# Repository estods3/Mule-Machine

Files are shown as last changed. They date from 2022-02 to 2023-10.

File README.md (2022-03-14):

# mule_machine
A drinkbot for making Moscow Mules

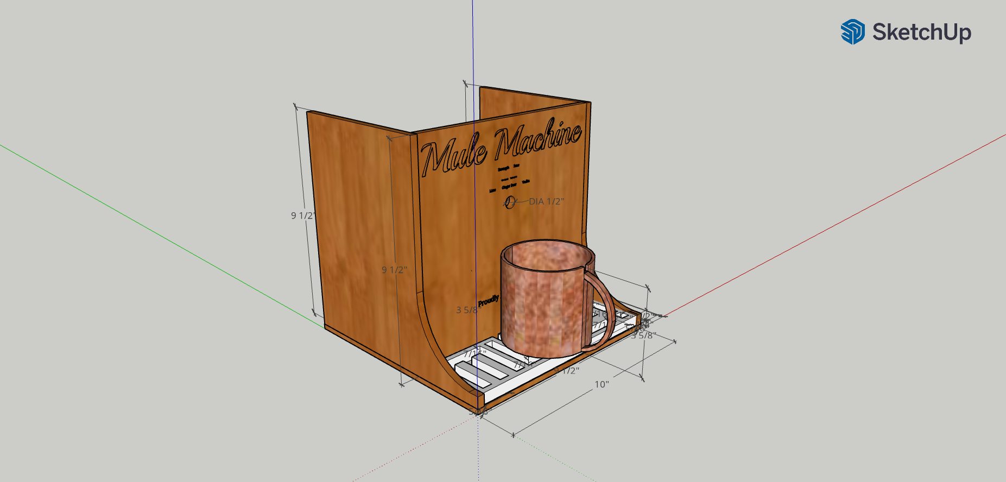
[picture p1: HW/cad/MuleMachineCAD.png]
CAD Assembly
[]()

## Design File Structure

### SW
ATmega328 microcontroller code.
  * Pin Assignments
  * Bootup Animation
  * Standby Animation
  * Potentiometer Calibration Controls
  * Cup-Sensor Detection
  * Pump Control and LED animation

### HW

#### cad

Sketchup File - 3D model

[CAD Assembly]()

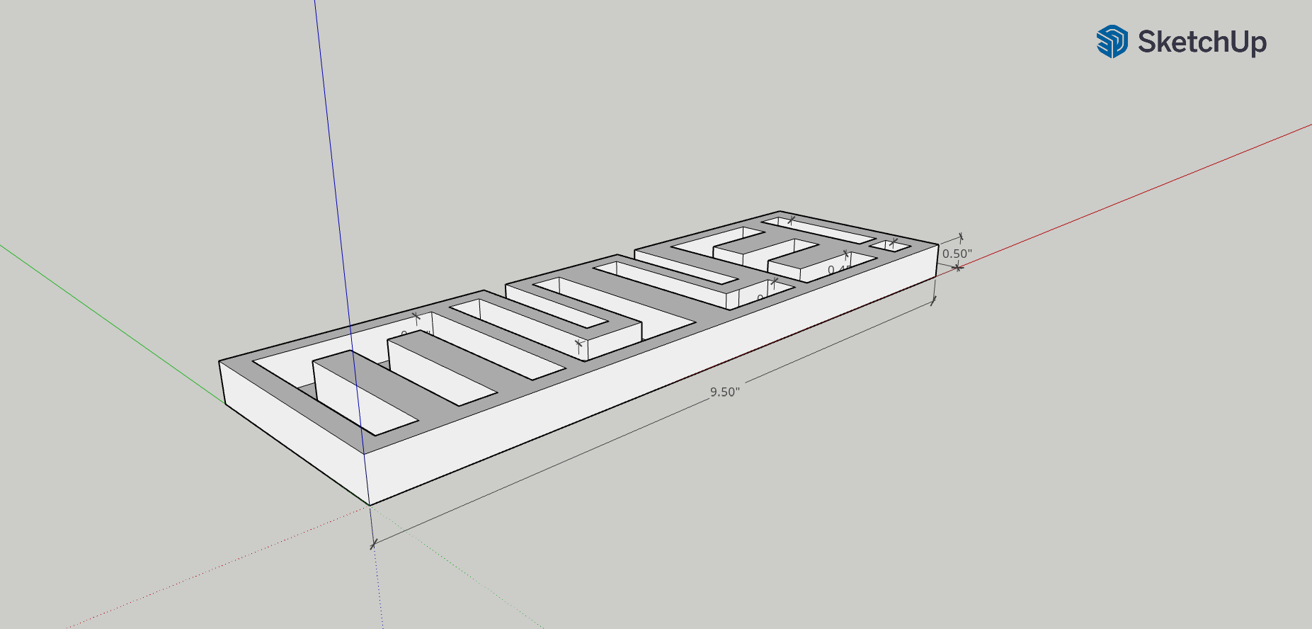
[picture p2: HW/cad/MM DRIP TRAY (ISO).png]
DRIP TRAY ISO
[]()
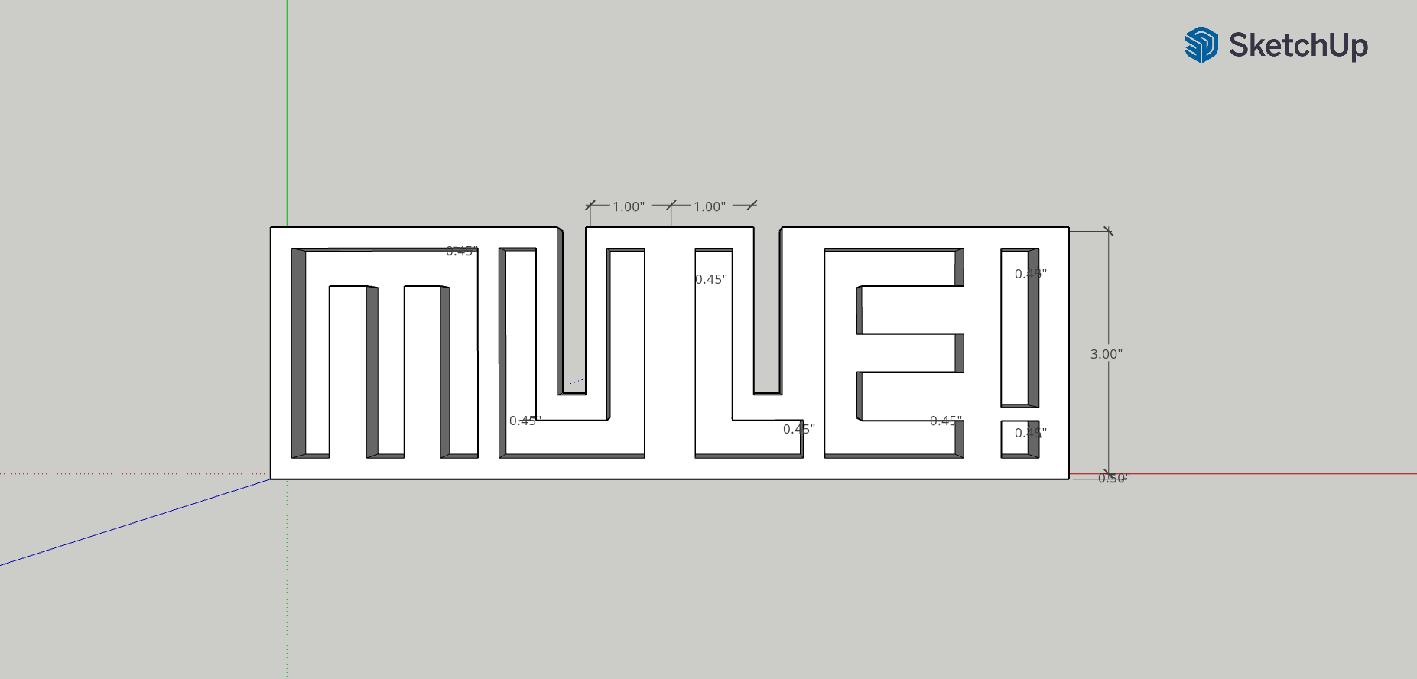
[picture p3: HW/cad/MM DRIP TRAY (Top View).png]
DRIP TRAY Top View
[]()

LightBurn laser engraved part files (Coming Soon)

3D printed part files
* MM DRIP TRAY.STL 

#### pcb

Eagle Schematic file

Eagle board layout file

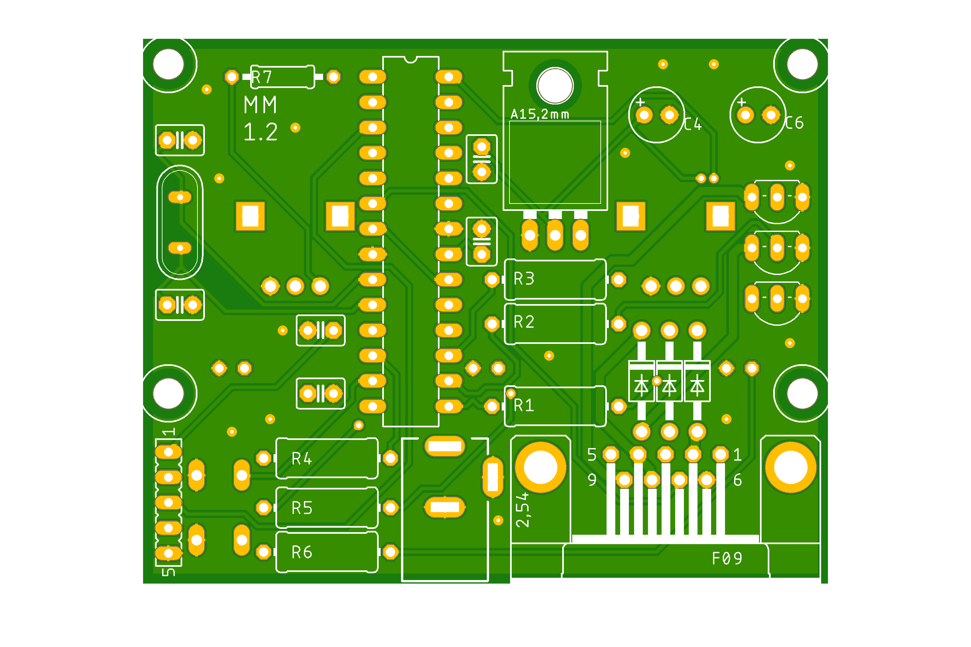
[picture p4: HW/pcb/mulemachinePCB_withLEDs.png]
PCB Top
[]()
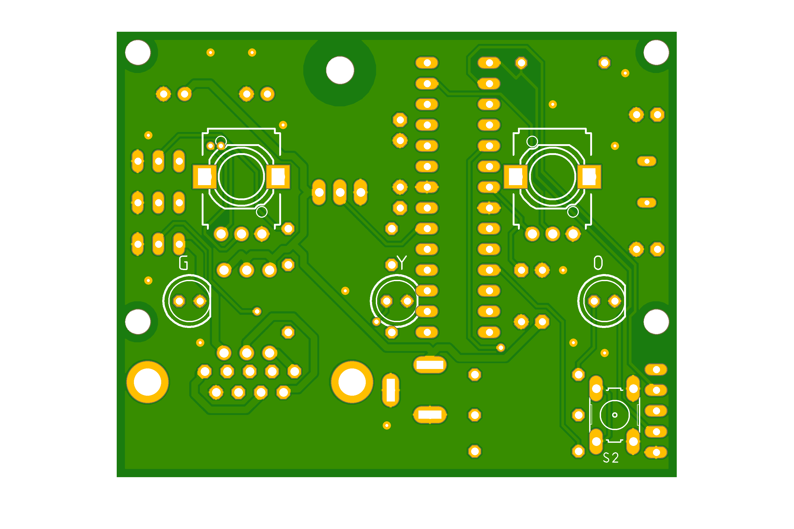
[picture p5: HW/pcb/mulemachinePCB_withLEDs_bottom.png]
PCB Bottom
[]()

associated gerber files (manufacturing)

parts list/BOM

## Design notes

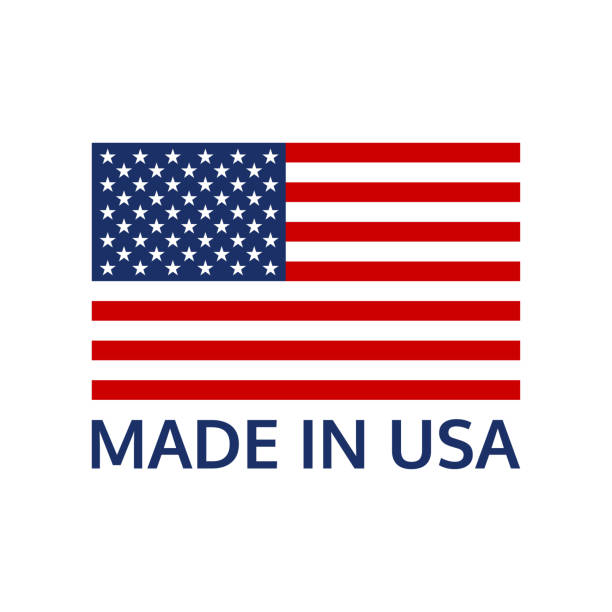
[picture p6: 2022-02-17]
HW/laser/american_flag.jpg

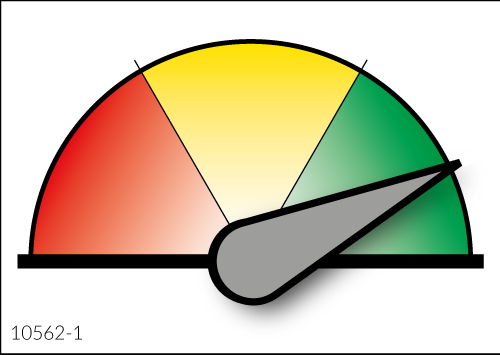
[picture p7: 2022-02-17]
HW/laser/gauge.png

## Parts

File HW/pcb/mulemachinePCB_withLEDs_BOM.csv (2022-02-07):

Part | Value | Device | Package | Description | MF | MPN | OC_FARNELL | OC_NEWARK | POPULARITY | SPICEPREFIX
C1 | 470uF | C2,5-3 | C2.5-3 | CAPACITOR |  |  |  |  | 38
C2 | 22pF | C2,5-3 | C2.5-3 | CAPACITOR |  |  |  |  | 38
C3 | 22pF | C2,5-3 | C2.5-3 | CAPACITOR |  |  |  |  | 38
D1 | 1N4004 | 1N4004 | DO41-10 | DIODE |  |  |  |  | 82
D2 | 1N4004 | 1N4004 | DO41-10 | DIODE |  |  |  |  | 82
D3 | 1N4004 | 1N4004 | DO41-10 | DIODE |  |  |  |  | 82
IC1 | LD117AV50 | LD117AV50 | TO220L1 | Low drop fixed and adjustable positive voltage regulators 1 A |  |  |  |  | 0
IC2 | MEGA8-P | MEGA8-P | DIL28-3 | MICROCONTROLLER |  |  | unknown | unknown | 17
J1 | DCJ0202 | DCJ0202 | DCJ0202 | DC POWER JACK |  |  | unknown | unknown | 17
LED1 |  | LED5MM | LED5MM | LED |  |  |  |  | 93
LED2 |  | LED5MM | LED5MM | LED |  |  |  |  | 93
LED3 |  | LED5MM | LED5MM | LED |  |  |  |  | 93
Q1 |  | XTAL/S | QS | CRYSTAL |  |  |  |  | 59
R1 | 150 | R-US_0204/7 | 0204/7 | RESISTOR, American symbol |  |  |  |  | 48 | R
R2 | 150 | R-US_0204/7 | 0204/7 | RESISTOR, American symbol |  |  |  |  | 48 | R
R3 | 150 | R-US_0204/7 | 0204/7 | RESISTOR, American symbol |  |  |  |  | 48 | R
R4 | 200 | R-US_0204/7 | 0204/7 | RESISTOR, American symbol |  |  |  |  | 48 | R
R5 | 200 | R-US_0204/7 | 0204/7 | RESISTOR, American symbol |  |  |  |  | 48 | R
R6 | 200 | R-US_0204/7 | 0204/7 | RESISTOR, American symbol |  |  |  |  | 48 | R
R7 | 200 | R-US_0204/7 | 0204/7 | RESISTOR, American symbol |  |  |  |  | 48 | R
S1 | RDT1034 | RDT1034 | RDT1034 | PUSH SWITCH |  |  |  |  | 4
SV1 |  | FE05-1 | FE05-1 | FEMALE HEADER |  |  | unknown | unknown | 7
T1 |  | MPS2222A-NPN-TO92-CBE | TO92-CBE | NPN Transistror |  |  |  |  | 0
T2 |  | MPS2222A-NPN-TO92-CBE | TO92-CBE | NPN Transistror |  |  |  |  | 0
T3 |  | MPS2222A-NPN-TO92-CBE | TO92-CBE | NPN Transistror |  |  |  |  | 0
X2 |  | F09HP | F09HP | SUB-D |  |  | unknown | unknown | 2

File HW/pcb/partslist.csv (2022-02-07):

Partlist
Exported from mulemachinePCB_withLEDs.sch at 2/1/22 5:24 PM
EAGLE Version 9.6.2 Copyright (c) 1988-2020 Autodesk, Inc.
Assembly variant:
Part     Value          Device                Package  Library        Sheet
C1       470uF          C2,5-3                C2.5-3   capacitor-wima 1
C2       22pF           C2,5-3                C2.5-3   capacitor-wima 1
C3       22pF           C2,5-3                C2.5-3   capacitor-wima 1
D1       1N4004         1N4004                DO41-10  diode          1
D2       1N4004         1N4004                DO41-10  diode          1
D3       1N4004         1N4004                DO41-10  diode          1
IC1      LD117AV50      LD117AV50             TO220L1  v-reg          1
IC2      MEGA8-P        MEGA8-P               DIL28-3  atmel          1
J1       DCJ0202        DCJ0202               DCJ0202  con-jack       1
LED1                    LED5MM                LED5MM   led            1
LED2                    LED5MM                LED5MM   led            1
LED3                    LED5MM                LED5MM   led            1
Q1       16Mhz          XTAL/S                QS       special        1
R1       150            R-US_0207/10          0207/10  rcl            1
R2       150            R-US_0207/10          0207/10  rcl            1
R3       150            R-US_0207/10          0207/10  rcl            1
R4       200            R-US_0207/10          0207/10  rcl            1
R5       200            R-US_0207/10          0207/10  rcl            1
R6       200            R-US_0207/10          0207/10  rcl            1
R7       200            R-US_0207/10          0207/10  rcl            1
R8       1k ohms        TRIM_EU-B25P          B25P     pot            1
R9       1k ohms        TRIM_EU-B25P          B25P     pot            1
S1       RDT1034        RDT1034               RDT1034  switch         1
SV1                     FE05-1                FE05-1   con-lsta       1
T1                      MPS2222A-NPN-TO92-CBE TO92-CBE transistor     1
T2                      MPS2222A-NPN-TO92-CBE TO92-CBE transistor     1
T3                      MPS2222A-NPN-TO92-CBE TO92-CBE transistor     1
X2                      F09HP                 F09HP    con-subd       1

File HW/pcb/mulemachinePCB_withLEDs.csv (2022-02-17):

Part | Value | Device | Package | Description | MF | MPN | OC_FARNELL | OC_NEWARK | POPULARITY | SPICEPREFIX
C1 | 0.1uF | C2,5-3 | C2.5-3 | CAPACITOR |  |  |  |  | 38
C2 | 22pF | C2,5-3 | C2.5-3 | CAPACITOR |  |  |  |  | 38
C3 | 22pF | C2,5-3 | C2.5-3 | CAPACITOR |  |  |  |  | 38
C5 | 470uF | CPOL-US153CLV-0605 | 153CLV-0605 | POLARIZED CAPACITOR, American symbol |  |  |  |  | 8 | C
D1 | 1N4004 | 1N4004 | DO41-10 | DIODE |  |  |  |  | 82
D2 | 1N4004 | 1N4004 | DO41-10 | DIODE |  |  |  |  | 82
D3 | 1N4004 | 1N4004 | DO41-10 | DIODE |  |  |  |  | 82
IC1 | LD117AV50 | LD117AV50 | TO220L1 | Low drop fixed and adjustable positive voltage regulators 1 A |  |  |  |  | 0
IC2 | MEGA8-P | MEGA8-P | DIL28-3 | MICROCONTROLLER |  |  | unknown | unknown | 17
J1 | DCJ0202 | DCJ0202 | DCJ0202 | DC POWER JACK |  |  | unknown | unknown | 17
LED1 |  | LED5MM | LED5MM | LED |  |  |  |  | 93
LED2 |  | LED5MM | LED5MM | LED |  |  |  |  | 93
LED3 |  | LED5MM | LED5MM | LED |  |  |  |  | 93
Q1 | 16Mhz | XTAL/S | QS | CRYSTAL |  |  |  |  | 59
R1 | 150 | R-US_0207/10 | 0207/10 | RESISTOR, American symbol |  |  |  |  | 36 | R
R2 | 150 | R-US_0207/10 | 0207/10 | RESISTOR, American symbol |  |  |  |  | 36 | R
R3 | 150 | R-US_0207/10 | 0207/10 | RESISTOR, American symbol |  |  |  |  | 36 | R
R4 | 200 | R-US_0207/10 | 0207/10 | RESISTOR, American symbol |  |  |  |  | 36 | R
R5 | 200 | R-US_0207/10 | 0207/10 | RESISTOR, American symbol |  |  |  |  | 36 | R
R6 | 200 | R-US_0207/10 | 0207/10 | RESISTOR, American symbol |  |  |  |  | 36 | R
R7 | 10k | R-US_0207/10 | 0207/10 | RESISTOR, American symbol |  |  |  |  | 36 | R
R10 | US-EVUF3L | US-EVUF3L | EVUFXL | 9 mm Square Rotary Potentiometers |  |  |  |  | 0
R11 | US-EVUF3L | US-EVUF3L | EVUFXL | 9 mm Square Rotary Potentiometers |  |  |  |  | 0
S1 | RDT1034 | RDT1034 | RDT1034 | PUSH SWITCH |  |  |  |  | 4
SV1 |  | FE05-1 | FE05-1 | FEMALE HEADER |  |  | unknown | unknown | 7
T1 |  | MPS2222A-NPN-TO92-CBE | TO92-CBE | NPN Transistror |  |  |  |  | 0
T2 |  | MPS2222A-NPN-TO92-CBE | TO92-CBE | NPN Transistror |  |  |  |  | 0
T3 |  | MPS2222A-NPN-TO92-CBE | TO92-CBE | NPN Transistror |  |  |  |  | 0
X2 |  | F09HP | F09HP | SUB-D |  |  | unknown | unknown | 2

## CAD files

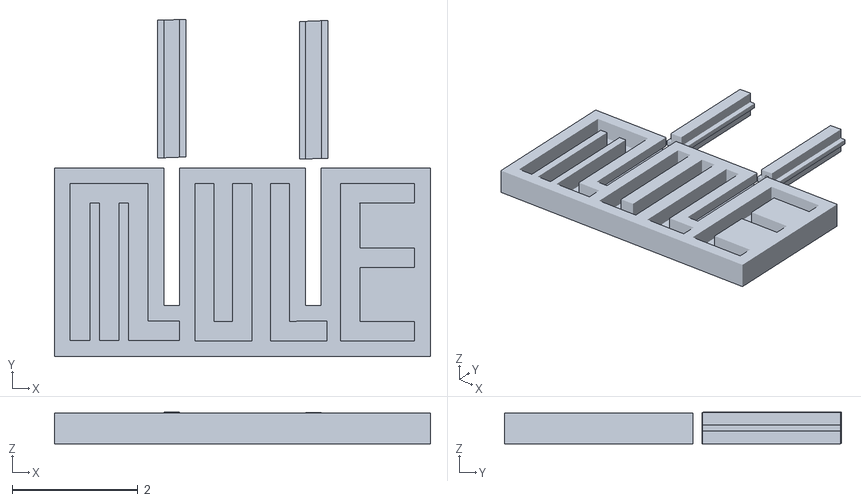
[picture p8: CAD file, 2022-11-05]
HW/cad/MM DRIP TRAY.stl
5.98 x 5.36 x 0.505

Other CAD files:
HW/cad/MM DRIP TRAY.skp
HW/cad/MuleMachineCAD.skp

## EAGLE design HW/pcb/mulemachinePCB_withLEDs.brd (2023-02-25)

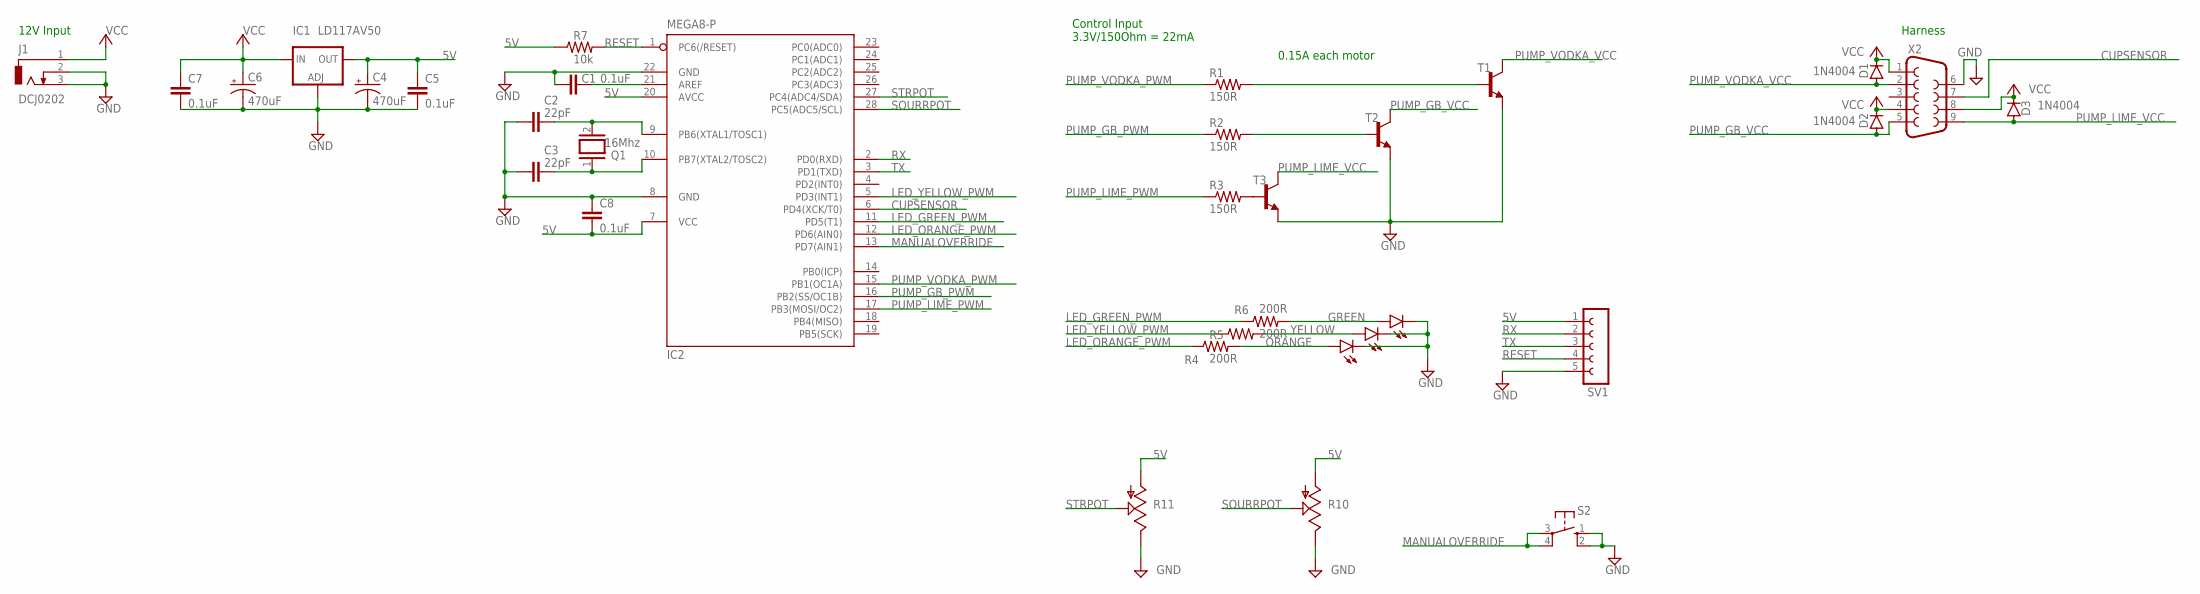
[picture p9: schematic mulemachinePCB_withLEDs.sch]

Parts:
C1, C5, C7, C8: 0.1uF; C2.5-3
C2, C3: 22pF; C2.5-3
C4, C6: 470uF; E2,5-6
D1, D2, D3: 1N4004; DO41-10
IC1: LD117AV50; TO220L1
IC2: MEGA8-P; DIL28-3
J1: DCJ0202
LED1, LED2, LED3: LED5MM
Q1: 16Mhz; QS
R1, R2, R3: 150R; 0411/12
R4, R5, R6: 200R; 0411/12
R7: 10k; 0207/10
R10, R11: US-EVUF3L; EVUFXL
S2: 10-XX; B3F-10XX
SV1: FE05-1
T1, T2, T3: 2N4401-NPN-TO92-EBC; TO92-EBC
X2: F09HP

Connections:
5V: C4.+, C5.1, C8.2, IC1.2 (OUT), IC2.7 (VCC), IC2.20 (AVCC), R7.1, R10.1 (A), R11.1 (A), SV1.1
CUPSENSOR: IC2.6 (PD4(XCK/T0)), X2.7
GND: C1.2, C2.2, C3.2, C4.-, C5.2, C6.-, C7.2, C8.1, IC1.1 (ADJ), IC2.8 (GND), IC2.22 (GND), J1.2, J1.3, LED1.K (C), LED2.K (C), LED3.K (C), R10.3 (E), R11.3 (E), S2.1 (S), S2.2 (S1), SV1.5, T1.E, T2.E, T3.E, X2.6
GREEN: LED3.A, R6.2
LED_GREEN_PWM: IC2.11 (PD5(T1)), R6.1
LED_ORANGE_PWM: IC2.12 (PD6(AIN0)), R4.1
LED_YELLOW_PWM: IC2.5 (PD3(INT1)), R5.1
MANUALOVERRIDE: IC2.13 (PD7(AIN1)), S2.3, S2.4 (P1)
unnamed: R3.2, T3.B
unnamed: R2.2, T2.B
unnamed: R1.2, T1.B
unnamed: C3.1, IC2.10 (PB7(XTAL2/TOSC2)), Q1.1
unnamed: C2.1, IC2.9 (PB6(XTAL1/TOSC1)), Q1.2
unnamed: C1.1, IC2.21 (AREF)
ORANGE: LED1.A, R4.2
PUMP_GB_PWM: IC2.16 (PB2(SS/OC1B)), R2.1
PUMP_GB_VCC: D2.A, T2.C, X2.5
PUMP_LIME_PWM: IC2.17 (PB3(MOSI/OC2)), R3.1
PUMP_LIME_VCC: D3.A, T3.C, X2.9
PUMP_VODKA_PWM: IC2.15 (PB1(OC1A)), R1.1
PUMP_VODKA_VCC: D1.A, T1.C, X2.2
RESET: IC2.1 (PC6(/RESET)), R7.2, SV1.4
RX: IC2.2 (PD0(RXD)), SV1.2
SOURRPOT: IC2.28 (PC5(ADC5/SCL)), R10.2 (S)
STRPOT: IC2.27 (PC4(ADC4/SDA)), R11.2 (S)
TX: IC2.3 (PD1(TXD)), SV1.3
VCC: C6.+, C7.1, D1.C, D2.C, D3.C, IC1.3 (IN), J1.1, X2.1, X2.4, X2.8
YELLOW: LED2.A, R5.2

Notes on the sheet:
12V Input
Harness
0.15A each motor
Control Input 3.3V/150Ohm = 22mA

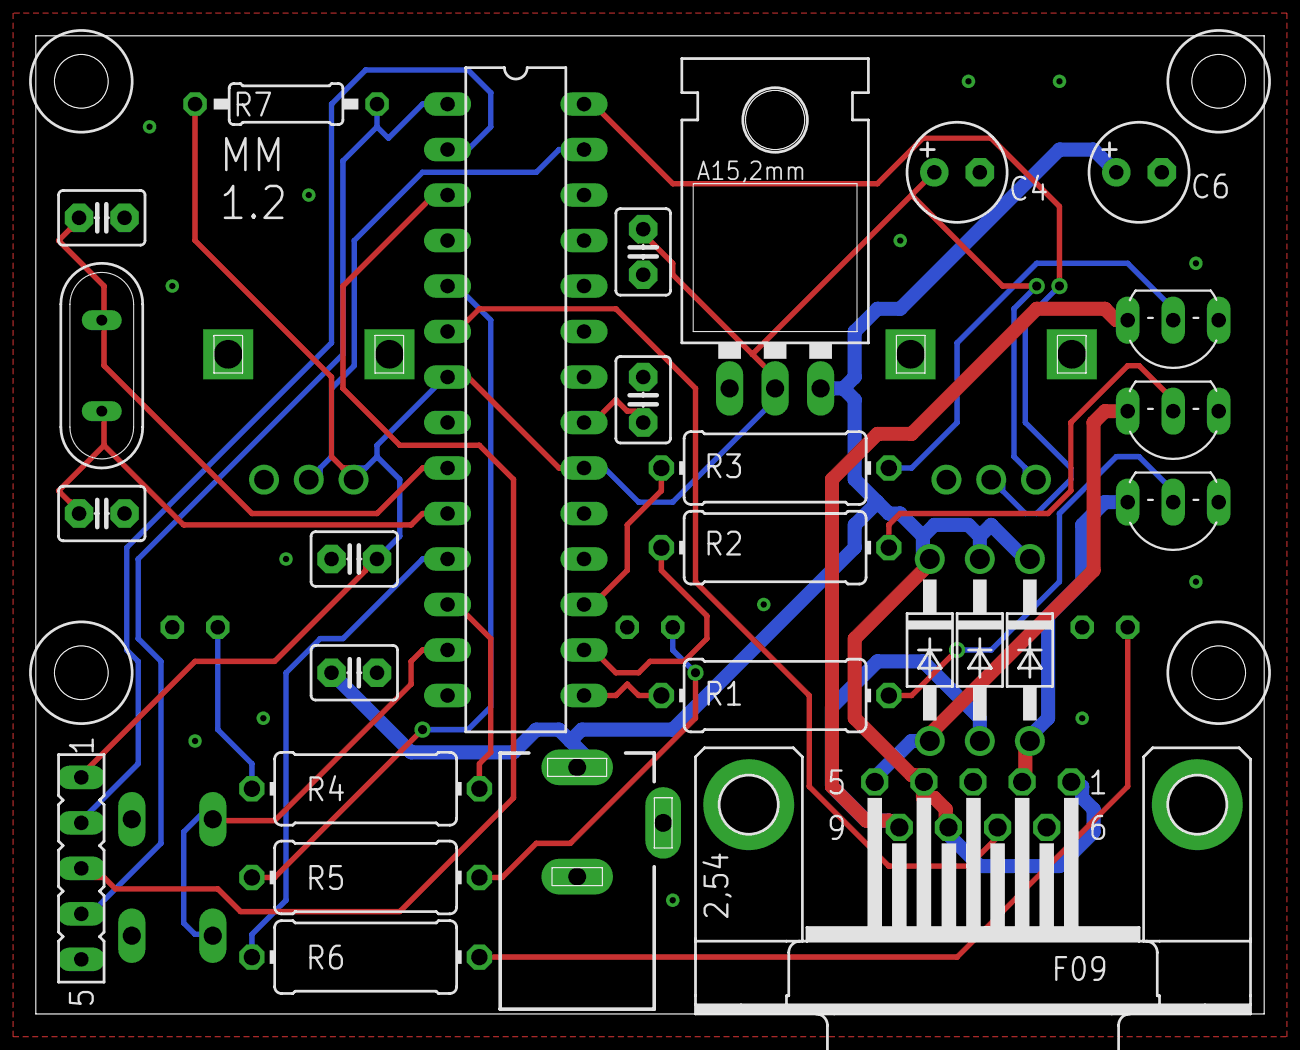
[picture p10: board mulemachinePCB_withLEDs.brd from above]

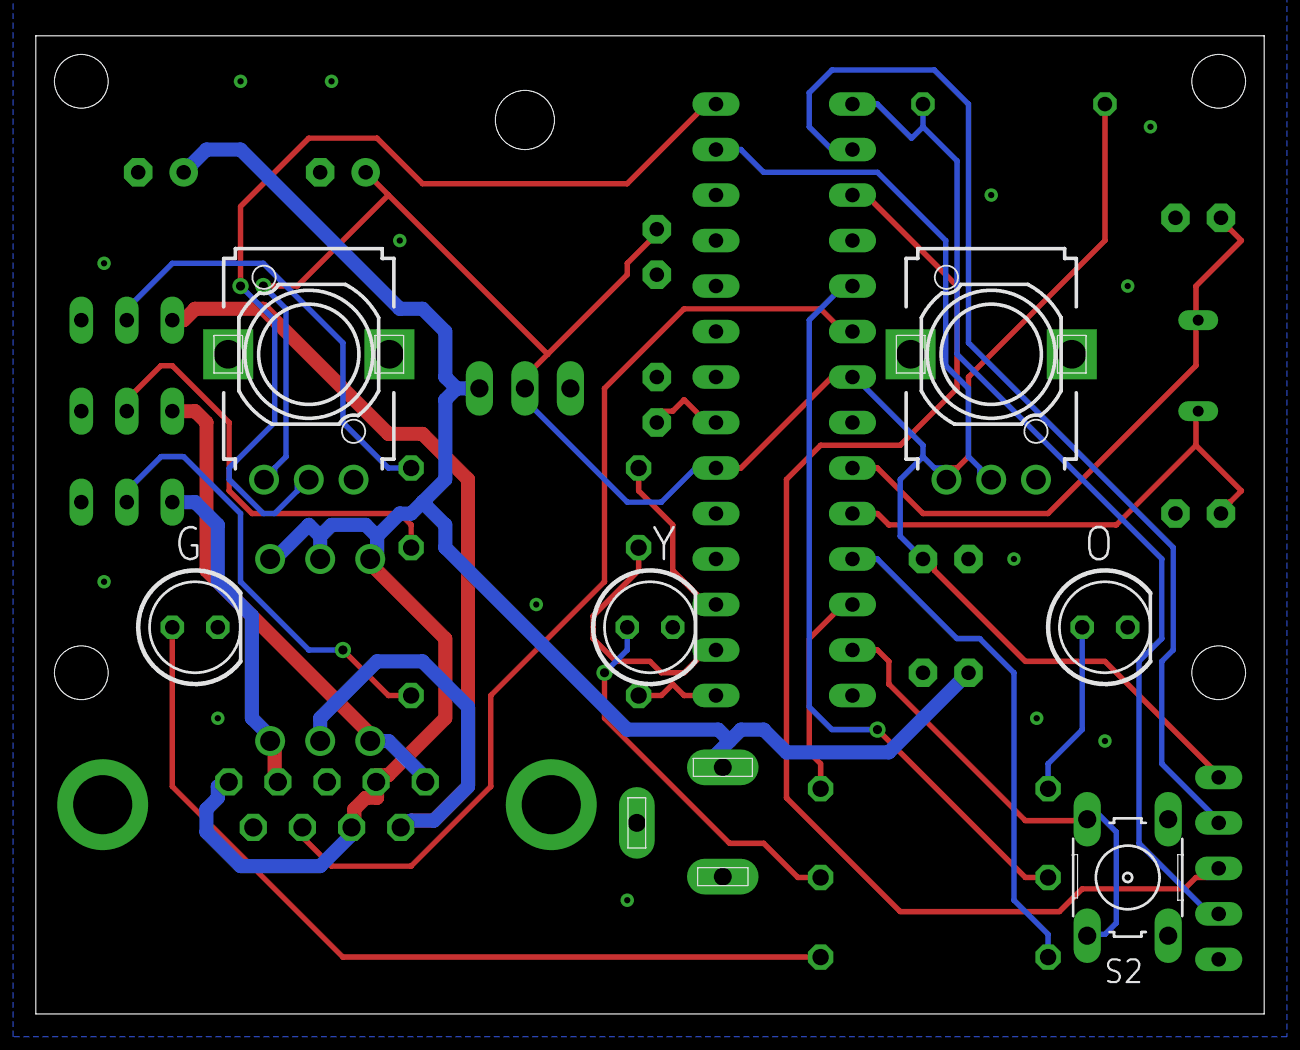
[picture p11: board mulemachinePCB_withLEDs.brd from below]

Board: 2 copper layers, 68.6 x 54.6 mm, 33 parts (6 on the bottom side), 28 nets.

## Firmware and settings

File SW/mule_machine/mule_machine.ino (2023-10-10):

//#include <SoftPWM.h>
//#include <SoftPWM_timer.h>

/*
 Mule Machine
 @Author: Evan Stoddart 
 Email: estods76@gmail.com Github: estods3
 Constants: Pinout and Calibration
 Setup: Initialize pins and variables, perform a bootup animation
 Loop: Perform Standby animation every few seconds, wait for cup to be placed on machine, make drink
*/

// PINOUT DEFINITION
//Buttons, LEDs, Pumps
//HARDWARE: <MM1.1
//inputs
//const int cup_present_buttonPin = 5; //PD5, physical pin 11                 
//const int manual_override_button_pin = 6; //PD6, physical pin 12
//const int tuner_strength_pin = A4; //PC4, physical pin 27
//const int tuner_sour_pin = A5; //PC5, physical pin 28
////outputs
//const int ledGreen_Lime = 2; // PD2, physical pin 4
//const int ledYellow_GingerBeer = 3; // PD3, physical pin 5
//const int ledOrange_Vodka = 4; // PD4, physical pin 6
//const int pump_Vodka = A1; //PC1,A1, physical pin 24
//const int pump_GingerBeer = A2; //PC2,A2, physical pin 25
//const int pump_Lime =  A3; //PC3,A3, physical pin 26

//TODO HARDWARE: MM1.2, change to use real PWM not SoftPWM Lib
//inputs
const int cup_present_buttonPin = 4; //PD4, physical pin 6                 
const int manual_override_button_pin = 7; //PD7, physical pin 13
const int tuner_strength_pin = A4; //PC4, physical pin 27
const int tuner_sour_pin = A5; //PC5, physical pin 28
//outputs (PWM)
const int ledGreen_Lime = 5; // PD5, physical pin 11
const int ledYellow_GingerBeer = 3; // PD3, physical pin 5
const int ledOrange_Vodka = 6; // PD6, physical pin 12
const int pump_Vodka = 9; //PB1, physical pin 15
const int pump_GingerBeer = 10; //PB2, physical pin 16
const int pump_Lime =  11; //PB3, physical pin 17

//ANIMATION DELAYS
//Bootup, Standby Mode, Mixing Mode
const int bootup_blink_duration = 100;
const int standby_blink_duration = 25;
const int standby_animation_interval = 3000;
const int mixingmode_starting_blink_duration = 100;

//PUMP CURRENT SPIKE DELAY
// prevent pumps drawing too much current from Arduino when turning on all at once.
const int current_spike_delay = 25;
// Number of motors: 3 (1 GB, 1 Lime, 1 Vodka) 4, (2 GB, 1 Lime, 1 Vodka)
const int num_motors = 4;
const int motor_deadzone = 200; // bottom !quarter of potentiometer results in PWM that isnt strong enought to rotate motors.

// MIXING MODE CALIBRATION
bool cup_is_present;
bool manual_override;
const int pour_duration_per_cycle = 150*4; //ms.

// Nominal Recipe
// 0.5 Cups per serving GB--> 2/3rd (let 2/3 = 100, so GB pump runs at 100%) of Drink should be Ginger Beer
// 0.0625 Cups per serving Lime --> Of remaining 1/3 (if 2/3 = 100, then 1/3 = 50), 1/4 (0.25) should be Lime
// 0.1875 Cups per serving Vodka --> Of remaining 1/3 (if 2/3 = 100, then 1/3 = 50), 3/4 (0.75) should be Vodka
// -----------------------------------------------------------------------
const int nominal_setting_ginger_beer = 100; //100%
const int nominal_setting_lime = (50) * 0.25 * (num_motors-2); //12.5%, if num_motors = 4, then double lime setting
const int nominal_setting_vodka = (50) * 0.75 * (num_motors-2); //37.5%, if num_motors = 4, then double vodka setting

int temp_analog_reading;
int temp_mapped_analog_reading;
const int numReadings  = 10;
int readings_strength[numReadings];
int readings_sour[numReadings];
int readIndex_sour;
int readIndex_strength;
int calibration_percentage_Lime;
int calibration_percentage_GingerBeer;
int calibration_percentage_Vodka;
int time_passed_ginger_beer_start; //calculation

//TODO numDrinksTilEmpty

// FUNCTION: setup()
void setup() {

  Serial.begin(9600);
  Serial.println(F("SUM,Vodka,Lime,GingerBeer")); 

  // set the input pins
  pinMode(tuner_strength_pin, INPUT);
  pinMode(tuner_sour_pin, INPUT);
  pinMode(cup_present_buttonPin, INPUT_PULLUP);
  pinMode(manual_override_button_pin, INPUT_PULLUP);
  // set the LEDs and Pumps as output
  pinMode(ledOrange_Vodka, OUTPUT);
  pinMode(ledYellow_GingerBeer, OUTPUT);
  pinMode(ledGreen_Lime, OUTPUT);
  //MMv1.2+
  pinMode(pump_Vodka, OUTPUT);
  pinMode(pump_GingerBeer, OUTPUT);
  pinMode(pump_Lime, OUTPUT);
  // Initialize calibration variables and get initial readings
  readings_strength[numReadings] = {};
  readings_sour[numReadings] = {};
  readIndex_sour = 0;
  readIndex_strength = 0;
  update_calibration_from_user_settings();

  // Initialize PWM Interface for LEDs and Pumps
  //MMv1.1
  //SoftPWMBegin();
  //SoftPWMSet(pump_Vodka, 0);
  //SoftPWMSet(pump_GingerBeer, 0);
  //SoftPWMSet(pump_Lime, 0);
  //SoftPWMSet(ledOrange_Vodka, 0);
  //SoftPWMSet(ledYellow_GingerBeer, 0);
  //SoftPWMSet(ledGreen_Lime, 0);
  //SoftPWMSetFadeTime(ALL, 0, 0);

  // Initial Digital Inputs as OFF (false)
  cup_is_present = false;
  manual_override = false;
  
  // Perform an LED Animation to let you know the machine is up and runnning
  animate_LEDs_for_set_time_OYG(' ', ' ', ' ', bootup_blink_duration);
  animate_LEDs_for_set_time_OYG('O', ' ', ' ', bootup_blink_duration);
  animate_LEDs_for_set_time_OYG(' ', 'Y', ' ', bootup_blink_duration);
  animate_LEDs_for_set_time_OYG(' ', ' ', 'G', bootup_blink_duration);
  animate_LEDs_for_set_time_OYG(' ', 'Y', ' ', bootup_blink_duration);
  animate_LEDs_for_set_time_OYG('O', ' ', ' ', bootup_blink_duration);
  animate_LEDs_for_set_time_OYG(' ', 'Y', ' ', bootup_blink_duration);
  animate_LEDs_for_set_time_OYG(' ', ' ', 'G', bootup_blink_duration);
  animate_LEDs_for_set_time_OYG(' ', 'Y', ' ', bootup_blink_duration);
  animate_LEDs_for_set_time_OYG('O', ' ', ' ', bootup_blink_duration);
  animate_LEDs_for_set_time_OYG(' ', 'Y', ' ', bootup_blink_duration);
  animate_LEDs_for_set_time_OYG(' ', ' ', 'G', bootup_blink_duration);
  animate_LEDs_for_set_time_OYG(' ', ' ', ' ', 0);
}

// FUNCTION: loop()
void loop() {
   update_calibration_from_user_settings();
  
  // STANDBY MODE (Heartbeat)
  // Perform a short animation every 3 seconds to let you know machine is alive
  animate_LEDs_for_set_time_OYG(' ', ' ', 'G', standby_blink_duration);
  animate_LEDs_for_set_time_OYG(' ', 'Y', ' ', standby_blink_duration);
  animate_LEDs_for_set_time_OYG('O', ' ', ' ', standby_blink_duration);
  animate_LEDs_for_set_time_OYG(' ', ' ', ' ', standby_animation_interval);

  //TODO if(numDrinksTilEmpty < 3) flash RED LED
  
  // Wait for Copper Cup (Button Press)
  // NOTE LOW=="CUP PRESENT" as the pull up resistor keeps the button value HIGH by default and pushing
  // the button creates a LOW signal.
  // When button pressed: call functions for Vodka, GB, and Lime to pour until button is unpressed.
  cup_is_present = digitalRead(cup_present_buttonPin) == LOW; // CUP_present && numDrinksTilEmpty > 0
  manual_override = digitalRead(manual_override_button_pin) == LOW;
  if (cup_is_present || manual_override) {
       // Initiate Mule Making:
       // show initialization animation
       animate_LEDs_for_set_time_OYG(' ', ' ', ' ', mixingmode_starting_blink_duration);
       animate_LEDs_for_set_time_OYG('O', 'Y', 'G', mixingmode_starting_blink_duration);
       animate_LEDs_for_set_time_OYG(' ', ' ', ' ', mixingmode_starting_blink_duration);
       animate_LEDs_for_set_time_OYG('O', 'Y', 'G', mixingmode_starting_blink_duration);
       animate_LEDs_for_set_time_OYG(' ', ' ', ' ', mixingmode_starting_blink_duration);
       animate_LEDs_for_set_time_OYG('O', 'Y', 'G', mixingmode_starting_blink_duration);
       animate_LEDs_for_set_time_OYG(' ', ' ', ' ', mixingmode_starting_blink_duration);
       animate_LEDs_for_set_time_OYG('O', 'Y', 'G', mixingmode_starting_blink_duration);
       animate_LEDs_for_set_time_OYG(' ', ' ', ' ', 0);
       while(cup_is_present || manual_override){
           
           update_calibration_from_user_settings();
           
           // START MIXING DRINK
           // Start by switching all pumps to "ON". 
           
           // use a current_spike_delay to prevent the current from spiking all at once 
           // and resetting the Arduino.
           
           //MMv1.1
           //SoftPWMSetPercent(ledYellow_GingerBeer, calibration_percentage_GingerBeer);
           //SoftPWMSetPercent(pump_GingerBeer, calibration_percentage_GingerBeer);
           //MMv1.2+
           analogWrite(ledYellow_GingerBeer, int((calibration_percentage_GingerBeer / 100.0) * 255));
           analogWrite(pump_GingerBeer, int((calibration_percentage_GingerBeer / 100.0) * 255));
           
           // PWM Vodka Pump (Speed Controlled by User)
           delay(current_spike_delay);
           //MMv1.1
           //SoftPWMSetPercent(ledOrange_Vodka, calibration_percentage_Vodka);
           //SoftPWMSetPercent(pump_Vodka, calibration_percentage_Vodka);
           //MMv1.2+
           analogWrite(ledOrange_Vodka, int((calibration_percentage_Vodka / 100.0) * 255));
           analogWrite(pump_Vodka, int((calibration_percentage_Vodka / 100.0) * 255));
           
           // PWM Lime Pump (Speed Controlled by User)
           delay(current_spike_delay);
           //MMv1.1
           //SoftPWMSetPercent(ledGreen_Lime, calibration_percentage_Lime);
           //SoftPWMSetPercent(pump_Lime, calibration_percentage_Lime);
           //MMv1.2+
           analogWrite(ledGreen_Lime, int((calibration_percentage_Lime / 100.0) * 255));
           analogWrite(pump_Lime, int((calibration_percentage_Lime / 100.0) * 255));
           
           time_passed_ginger_beer_start = 2*current_spike_delay;
           if((pour_duration_per_cycle - time_passed_ginger_beer_start) > 0){
               delay(pour_duration_per_cycle - time_passed_ginger_beer_start);
           }

           //Read User Input for Mixing Mode
           cup_is_present = digitalRead(cup_present_buttonPin) == LOW;
           manual_override = digitalRead(manual_override_button_pin) == LOW;
       }
       //MMv1.2+
       analogWrite(pump_GingerBeer, int(0));
       analogWrite(pump_Vodka, int(0));
       analogWrite(pump_Lime, int(0));
       //MMv1.1
       //SoftPWMSetPercent(ALL, 0);
  }
}

/// ---------
/// FUNCTIONS
/// ---------
/*
 * FUNCTION: animate_LEDs_for_set_time_OYG 
 * DEF: perform an animation using all three LEDs.
 */
void animate_LEDs_for_set_time_OYG(char O_LED, char Y_LED, char G_LED, int delay_time) {
  if(O_LED == 'O'){ digitalWrite(ledOrange_Vodka, HIGH); } else{ digitalWrite(ledOrange_Vodka, LOW); }
  if(Y_LED == 'Y'){ digitalWrite(ledYellow_GingerBeer, HIGH); } else{ digitalWrite(ledYellow_GingerBeer, LOW); }
  if(G_LED == 'G'){ digitalWrite(ledGreen_Lime, HIGH); } else{ digitalWrite(ledGreen_Lime, LOW); }
  delay(delay_time);
}

/*
 * FUNCTION: update_calibration_from_user_settings 
 * DEF: update the calibration percentages from the users settings using potentiometers.
 */
void update_calibration_from_user_settings(){
  // Update Recipe from Calibration
  // (READ numReadings numer of samples from pots)
  for(int i=1; i< numReadings; i++){
    calibration_percentage_Vodka = smooth_strength();
    calibration_percentage_Lime = smooth_sour();
  }
  calibration_percentage_GingerBeer = 100; //133 - calibration_percentage_Vodka - calibration_percentage_Lime;
  
  //Error Checking
  if(calibration_percentage_GingerBeer > 100){
     calibration_percentage_GingerBeer = 100;
  }
  if(calibration_percentage_Vodka > 100){
     calibration_percentage_Vodka = 100;
  }
  if(calibration_percentage_Lime > 100){
     calibration_percentage_Lime = 100;
  }

  // DEBUG INTERFACE (Using Arduino Serial Monitor)
  Serial.print(calibration_percentage_GingerBeer + calibration_percentage_Lime + calibration_percentage_Vodka);
  Serial.print(',');
  Serial.print(calibration_percentage_Vodka);
  Serial.print(',');
  Serial.print(calibration_percentage_Lime);
  Serial.print(',');
  Serial.println(calibration_percentage_GingerBeer);
}

/*
 * FUNCTION: smooth_sour 
 * DEF: performs moving average on sour potentiometer.
 */
//NOTE: output is flipped max-to-low to match 5V and GND placement on schematic (5V should be on left pin when facing POT)
int smooth_sour() { /* function smooth */
  // read the sensor into the next position in the array
  temp_analog_reading = analogRead(tuner_sour_pin);
  if(temp_analog_reading < motor_deadzone) {
    temp_analog_reading = 0;
  }
  temp_mapped_analog_reading = map(temp_analog_reading, 0, 1023, 2.5*nominal_setting_lime, 0);
  readings_sour[readIndex_sour] = temp_mapped_analog_reading;
  readIndex_sour = readIndex_sour + 1;
  if (readIndex_sour >= numReadings) {
    readIndex_sour = 0;
  }
  
  // Compute Total of all Readings
  int total = 0;
  for(int i=0; i < numReadings; i++){
    total = total + readings_sour[i];
  }
  // Calculate the Average
  long average = total / numReadings;
  return average;
}

/*
 * FUNCTION: smooth_strength
 * DEF: performs moving average on strength potentiometer.
 */
//NOTE: output is flipped max-to-low to match 5V and GND placement on schematic (5V should be on left pin when facing POT)
int smooth_strength() { /* function smooth */
  // read the sensor into the next position in the array
  temp_analog_reading = analogRead(tuner_strength_pin);
  if(temp_analog_reading < motor_deadzone) {
    temp_analog_reading = 0;
  }
  temp_mapped_analog_reading = map(temp_analog_reading, 0, 1023, 2*nominal_setting_vodka, 0);
  readings_strength[readIndex_strength] = temp_mapped_analog_reading;
  readIndex_strength = readIndex_strength + 1;
  if (readIndex_strength >= numReadings) {
    readIndex_strength = 0;
  }
  
  // Compute Total of all Readings
  int total = 0;
  for(int i=0; i < numReadings; i++){
    total = total + readings_strength[i];
  }
  // Calculate the Average
  int average = total / numReadings;
  return average;
}

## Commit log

2022-02-07 added PCB Eagle files
    [DRILEGEND.CFG, mulemachinePCB_withLEDs.brd, mulemachinePCB_withLEDs.sch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]
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2022-02-07 added Sketchup File. updated README.
    [Mule Machine RevC.skp]
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2022-02-07 cleanup old pcd files
    [mulemachinePCB_withLEDs.brd]
2022-02-09 implemented new calibration with pots. not yet tested on HW
2022-02-09 added laser files for front and sides. not yet finished
2022-02-12 finished layout for PCB. implemented trace widths for PWR and GND. Lined up hole placement to match with Front panel laser design.
    [mulemachinePCB_withLEDs.brd, mulemachinePCB_withLEDs.sch]
2022-02-12 renamed MuleMachineCAD sketchup file
    [MuleMachineCAD.skp]
2022-02-12 finished preliminary design of front panel. need to determine assembly strategy for panels
2022-02-17 updated mule machine firmware to include better pot logic with rolling average (10 point). Tested on testbench with consistent results. Motors under load, Power consumption on standby was 0.8A @12V, 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
2022-02-17 ordered MM v1.0 of PCB. Gerber files contained in HW/pcb/mulemachinePCB_withLEDs_2022-02-17.zip
    [mulemachinePCB_withLEDs.brd, mulemachinePCB_withLEDs.csv, mulemachinePCB_withLEDs.sch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]
2022-02-24 fixed issue #7 on PCB. not yet ordered or tested on physical HW. schematic functionality should not change. just modified capacitor packaging
    [mulemachinePCB_withLEDs.brd, mulemachinePCB_withLEDs.sch]
2022-02-24 fixed HMI to better match 300 degree pots from PCB
2022-03-01 changed hole sizes for PCB mounting holes. adjusted sizes of pot and LED holes based on a test print
    [mulemachinePCB_withLEDs.brd]
2022-03-01 added offset to either side of laser front design to allow for slotted insert into sides
2022-03-01 first test of laser/front.lbrn2 file on 0.25 inch panel. Adjusted settings for text, image, holes, and title. all look good on test print. holes not all the way through wood.
2022-03-01 lowered speed/power for drill holes in laser CAD, as holes will not actually drill all the way through, and just serve as markings.
2022-03-01 fixed issue #8 where the transistor pinout was backwards. fixed for next PCB order
    [mulemachinePCB_withLEDs.brd, mulemachinePCB_withLEDs.sch]
2022-03-11 changed resistor packaging to 0411/12 for new 100 and 200 ohm 2Watt resistors purchased.
    [mulemachinePCB_withLEDs.sch]
2022-03-11 changed resistor packaging to 0411/12 for new 100 and 200 ohm 2Watt resistors purchased. change hole size (to 3mm) and spacing to match new pump mounting hole size for front panel.
2022-03-11 added gray outlines in panel for 6mm head size of new bolts.
2022-03-14 finished design of drip tray. imported into MuleMachineCAD file as component
    [MM DRIP TRAY.skp, MM DRIP TRAY.stl, MuleMachineCAD.skp]
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2022-03-15 lowered pump atttachment points to make more room for copper nozzle. made seperate layer for front panel outline
2022-03-18 moved copper nozzle to be side-by-side with PCB UI. adds more height and uses the space better. added filled holed at center of each hole to make a divit for using a drill bit
2022-03-18 committing changes to PCB layout before changing db9 location
    [mulemachinePCB_withLEDs.brd]
2022-03-24 preparing files for first prototype of version 1.0 of Mule Machine. Corrected Code to reflect Orange and Green LEDs being flipped on PCB and Code. Used PCB Version. Added some new design features to 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
    [mulemachinePCB_withLEDs.brd, mulemachinePCB_withLEDs.sch]
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2022-04-04 fixed #13 with additional 100uF cap on 12V power line and 0.1uF cap on 5v line in parallel with 470uF cap. This smooths the 12V line and the 5V line for more powerful motors. needs more duration of b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
    [mulemachinePCB_withLEDs.brd, mulemachinePCB_withLEDs.sch]
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2022-04-26 sourced push button and added to schematic and PCB layout. matched needed mounting to laser front panel cutout.
    [mulemachinePCB_withLEDs.brd, mulemachinePCB_withLEDs.sch]
2022-04-27 finished mating between front panel and PCB. routed PCB. PCB v1.1 is ready for gerber file generation and order.
    [mulemachinePCB_withLEDs.brd, mulemachinePCB_withLEDs.sch]
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2022-05-25 changed 12V side cap C6 to 470uF. rerouted board
    [mulemachinePCB_withLEDs.brd, mulemachinePCB_withLEDs.sch]
2022-06-10 added comments. changed new cal input time to 600ms. increased ramp up and ramp down times for PCM. chip reset issue still prevelant
    [mule_machine.ino]
2022-09-20 added decoupling cap for MCU to schematic. organized schematic with groups
    [mulemachinePCB_withLEDs.brd, mulemachinePCB_withLEDs.sch]
2022-09-21 rotated MCU to allow for better routing. added top and bottom layer ground planes with vias connecting them.
    [mulemachinePCB_withLEDs.brd, mulemachinePCB_withLEDs.sch]
2022-09-21 adjusted net classes so that pump VCCs lines were also considered power traces (wider). rerouted and adjusted GND planes
    [mulemachinePCB_withLEDs.brd, mulemachinePCB_withLEDs.sch]
2022-09-21 repinned LED and pump pins on MCU to use PWM digital pins. need to check and then reroute PCB and redo GND planes
    [mulemachinePCB_withLEDs.brd, mulemachinePCB_withLEDs.sch]
2022-09-21 reorganized MCU code. added a function for LED animations to clean up code. re-wrote analog moving filter functions to recompute total each run using array for() loop. need to test
2022-09-21 finished positioning components, rerouted and made ground planes
    [mulemachinePCB_withLEDs.brd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]
2022-09-21 finished positioning components, rerouted and made ground planes, added GND plane vias
    [mulemachinePCB_withLEDs.brd]
2022-10-07 updated code to include functions for LED animations. Tested on PCBs MMv1.1. working correctly, still experiencing issue #13 but not as frequently. MM can run for 30s+ before restarting
    [mule_machine.ino]
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2022-10-17 improved drip tray. reduced size, added T-Slot mounts.
    [MM DRIP TRAY.stl]
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2022-11-04 moved Y label for yellow LED on PCB. remake gerber files
    [mulemachinePCB_withLEDs.brd]
2022-11-05 fixed issue with mismatch in names for orange LED signal PWM signal name. corrected, regenerated CAM data, reordered PCBs, and remade PNGs
    [mulemachinePCB_withLEDs.brd, mulemachinePCB_withLEDs.sch]
2022-12-03 misc changes to laser program
    [mulemachinePCB_withLEDs.brd]
2022-12-03 added analogWrite() function calls for native PWM pins instead of using softPWM library. test on MM1.2 HW. working with LEDs not tested with pump harness. Observation: when in standby after power up 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
2023-02-25 fixed @21. added analogWrite(pump_*, 0) after while() loop to turn off pumps after exiting Mixing Mode
    [mule_machine.ino]
2023-02-25 fixed #21. added analogWrite(pump_*, 0) after while() loop to turn off pumps after exiting Mixing Mode
    [mule_machine.ino]
2023-10-10 added deadzone logic for motors. added mode to support 2 motors for ginger beer ingredient which allows for faster operation.
